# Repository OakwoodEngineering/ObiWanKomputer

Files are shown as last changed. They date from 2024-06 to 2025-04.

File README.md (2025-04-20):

# Obi Wan Komputer and Combined Payload Board
## Oakwood Engineering, NyanSat Project

Welcome to the public git repository for NyanSat's OBC and payload board.  We hope that this project will be generally useful for the CubeSat community.  NyanSat is a 2U CubeSat selected by NASA's CubeSat Launch Initiative and made by high school students at [Oakwood School](https://oakwoodway.org).

[NyanSat Obi Wan Komputer and Combined Payload Board](https://github.com/OakwoodEngineering/ObiWanKomputer) by [Oakwood Engineering](https://nyansat.org) is licensed under [Creative Commons Attribution-ShareAlike 4.0 International](https://creativecommons.org/licenses/by-sa/4.0/?ref=chooser-v1)    

It is based on the [PyCubed](https://pycubed.org) flight computer by Max Holliday.

The design was made with [Kicad EDA](https://www.kicad.org/) version 8 and is in the hardware directory.  More details to come.

For now, an overview of the design is in the following poster presented at Cal Poly's [CubeSat Developer Workshop](https://www.cubesatdw.org/) 2025 (click for PDF):

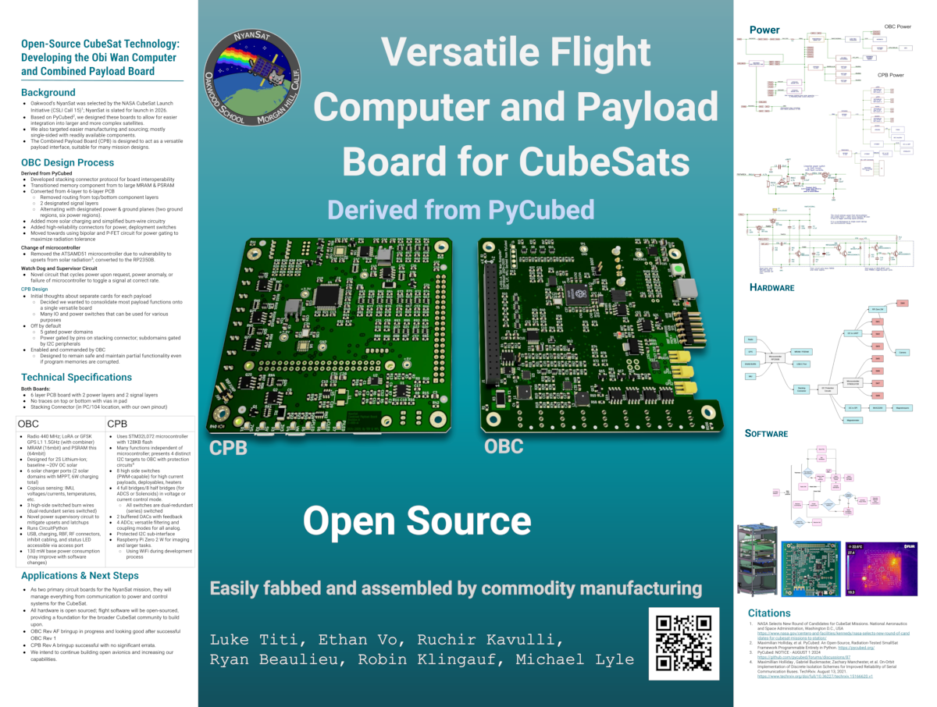
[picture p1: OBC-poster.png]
OBC Poster


You can also visit our website at [nyansat.org](https://nyansat.org).

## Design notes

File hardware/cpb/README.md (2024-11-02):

# NyanSat
## Combined Payload Board

The Combined Payload Board (CPB) is a component of the NyanSat project, designed to interface with a variety of payloads, including imaging, material science experiments, the Attitude Determination and Control Subsystem (ADACS), and the acoustic spacecraft mapping subsystem.

### Internal Interfaces
* Mechanical: PC/104 form factor for holes and board outline.
    * SMT components all on bottom side of board; top side for connectors and stacking Raspberry Pi Zero 2W.
* 40 pin spacecraft electrical bus
	* Battery voltage (post-inhibit switches, current sensing, current limiting on OBC).
	* One GPIO: Gating of battery voltage to board except bridge driver
    * One GPIO: Gating of battery voltage to bridge driver
	* I2C
		* I2C-UART Address: `0x90 = 1001 0000`
            * Raspberry Pi: controlled by serial from I2C-UART.
            * Pi power controlled by I2C-UART GPIO
            * 3 external power switches controlled by I2C-UART GPIOs.
        * I2C-SPI converter for driver bridges `0x50 = 0101 000X`
            * MAX22200 bridge chip select, command select, and enable controlled by I2C-SPI converter.
		* Microcontroller Address: TBD
	* Ground/return path for power and all signals
* Mounting holes
	* 0603 pads from holes to board ground exist; can populate with capacitor (AC-couple to stack), resistor, short, or leave open.

### External Interfaces
* 4 versatile analog inputs. provided by microcontroller ADC, 0-3.3V 12 bit 1.1MSPS.  Pads on board allow selections of various modes:
	* Divided voltage or pulled towards chosen voltage
	* Resistive termination or known impedance
	* AC coupling
    * Pin alternate functions allow use for digital inputs or timer outputs
* 2 DC (0-5V) or AC-coupled waveform generation channels produced from microcontroller DAC with ~40mA drive capability
	* Controlled by microcontroller; feedback to ADC allows precise control of voltages.
	* Low pass filter: 2nd order with -3dB bandwidth of 100KHz.
* 8 high-side switches of battery voltage for payloads and magnetorquers
	* 3 controlled by GPIO from I2C-UART peripheral
	* 1 controlled by onboard Raspberry Pi computer
	* 4 controlled by onboard Cortex-M0+ microcontroller
* 8 half-bridges with programmable current limits
* 5 pin connection for external I2C peripheral (e.g. magnetometer)
* On Pi: CSI interface for Raspberry Pi camera

### Anticipated Use
* Attitude Determination and Control Subsystem (ADACS):
	* Switches: 3 magnetorquers, bipolar (6 half-bridges)
* Acoustic Spacecraft Sounding:
	* Switch: Solenoid, driven by pair of half-bridges
	* Possible switch: MEMS microphone power
	* ADC: 2 channels of MEMS microphone.
* Material science / semiconductor characterization experiment  
	* Waveform generation: 2 channels of drive voltages.
	* ADC: 2 channels of measurement.
* Camera
	* Pi/CSI to camera.
	* Possible high powered LED via high side driver.
* Deployables
	* Option open to use high-side switches channels from here for deployment.
	* Consider using this board to energize second deployable resistor for redundancy.

### Stored-Program Computing Components
* Microcontroller; used mostly as a smart ADC/DAC.
	* STM32L072RBT6; 32MHz Cortex-M0+ with single-cycle multiplier, 128k flash, 6k data EEPROM, 20k RAM.
* Raspberry Pi Zero 2W; used mostly as interface for camera.
	* Quad-core Cortex A53 64-bit processor, 512MB SDRAM.
	* Wireless capabilities (disabled in flight) can be used for ground troubleshooting.
	* Use SLC microSD card, e.g. SFSD2048N1BN1WI-E-QF-111-STD from SwissBit.

### Design Philosophy
* Board's power is gated and will be completely de-powered if a pin on spacecraft electrical bus is not driven high.
* Seperate power gate for magnetorquer full-bridge.
* No high-level sequencing of experiments performed by this board; enabled and commanded from main On-Board Computer (OBC).
* I2C is isolated from spacecraft bus if de-powered or peripheral locks up.
* Large portions of functionality work even if non-volatile memory on a device is corrupted.
	* I2C-UART/GPIO chip does not have nonvolatile memory, and directly controls 4 output switches.
    * I2C-SPI and MAX22200 do not have nonvolatile state.
	* Microcontroller starts up held in reset until explicitly enabled by I2C-UART.
	* If microcontroller is corrupted, Raspberry Pi is capable of reprogramming via on-chip debug features.
    * Pi's power supply is separately enabled by I2C-UART.
	* If Pi filesystem is corrupted, small chance of recovery through failsafe pin (indicates to boot from different part of SD card).

### Known Weaknesses & Shortcomings
* No provision to measure power used by this board.
* No real current limiting beyond master current limiting from ADM1176 PMIC on OBC.
	* But: If entire satellite resets due to overcurrent, this board will revert to default state (turned off).
    * 200 mohm resistors and FET Rds do provide a little bit of mitigation of catastrophes.
* Raspberry Pi must be turned on to generate waveforms / run matsci experiment due to board architecture (needs 5V rail).
* Only having 4 ADC is a little limiting.

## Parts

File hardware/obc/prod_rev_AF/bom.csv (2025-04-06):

Designator | Footprint | Quantity | Value | LCSC Part #
C1, C12 | 0603 | 2 | 3.3nF | C1613
C10, C2, C28, C46, C49, C50, C6, C61, C65 | 0603 | 9 | 4.7uF | C19666
C11, C17, C21, C29, C31, C33, C36, C37, C38, C39, C40, C41, C42, C43, C44, C45, C47, C48, C52, C54, C59, C60, C9 | 0603 | 23 | 0.1uF | C1591
C13, C22, C3, C30 | 0603 | 4 | 10nF | C1589
C14, C16, C34, C51, C55, C62, C7 | 0603 | 7 | 1uF | C59782
C15, C23 | 0603 | 2 | 10uF35V | C194427
C18, C19, C35, C4, C56, C67, C68 | 0603 | 7 | 22uF | C2762594
C20, C24, C25 | 0603 | 3 | 15pF | C107037
C26, C8 | 0603 | 2 | 2.2uF | C23630
C27, C5 | 0603 | 2 | 22nF | C21122
C32 | 0805 | 1 | 47uF | C124129
C53, C57, C58, C64, C66 | 0603 | 5 | 10uF | C344022
C63 | 0603 | 1 | 47nF | C1622
D1 | D_SOD-323 | 1 | BAT20JFILM | C155590
D2 | 0805 | 1 | RED | C84256
D3 | LED_WS2812B_PLCC4_5.0x5.0mm_P3.2mm | 1 | WS2812B-B/W | C2874885
D4 | 0805 | 1 | GREEN | C2297
H1, H2, H3, H4 | MountingHole_3.2mm_M3_DIN965_Pad | 4 | MountingHole_Pad
J1 | PinHeader_2x20_P2.54mm_Vertical | 1 | Conn_02x20_Odd_Even
J2 | PinHeader_1x02_P2.00mm_Vertical | 1 | Conn_01x02
J3 | PinHeader_1x05_P2.54mm_Vertical | 1 | Conn_01x05
J301 | MMCX-6_UMPT-06-01-L-RA-WT-TR_P2.0mm | 1 | Inhibit Switches
J302 | Harwin_G125-FV104F3-02AB000P_P1.25mm_Vertical | 1 | Battery Pack
J4 | PinHeader_1x02_P2.00mm_Vertical | 1 | Conn_01x02
J5 | SAMTEC_MMCXV-J-P-HF-ST-EM1 | 1 | GPS2
J6 | SAMTEC_MMCXV-J-P-HF-ST-EM1 | 1 | GPS1
J7 | SAMTEC_MMCXV-J-P-HF-ST-EM1 | 1 | RADIO
J8 | PinHeader_1x06_P2.54mm_Horizontal | 1 | Conn_01x06
J9 | USB_C_Receptacle_G-Switch_GT-USB-7010ASV | 1 | USB_C_Receptacle_USB2.0 | C2988369
JP300 | CONN_22-11-2032_MOL | 1 | VBURN1
JP301 | CONN_22-11-2032_MOL | 1 | VBURN2
JP302 | CONN_22-11-2032_MOL | 1 | VBURN3
JP303, JP304, JP305 | CONN_22-11-2032_MOL | 3 | VS
JP306, JP307, JP308 | CONN_22-11-2032_MOL | 3 | VS2
L1, L3 | TDK VLCF5020T-330MR62-1 | 2 | 33uH | C2043695
L2, L5 | L_TDK_1008_2.5x2.0mm | 2 | 3.3uH | C404805
L4 | L_pol_2016 | 1 | 3.3uH | C42411119
Q1 | SOIC-8_3.9x4.9mm_P1.27mm | 1 | IRF7306 | C537809
Q10, Q2, Q4, Q6 | SOT-363_SC-70-6 | 4 | BSS138PS,115 | C193381
Q11, Q3, Q5, Q7, Q8, Q9 | SOT-363_SC-70-6 | 6 | MBT2222ADW1T1 | C157366
Q12, Q13, Q21 | SOT-23 | 3 | PMBT2222A | C23869
Q14, Q16, Q19, Q20, Q22 | SOIC-8_3.9x4.9mm_P1.27mm | 5 | IRF9393 | C520642
Q15, Q17, Q18 | SOT-23 | 3 | IRLML2803 | C2590
R1, R106, R107, R2 | 0603 | 4 | DNI
R10, R33, R53, R7 | 0603 | 4 | 680 | C112310
R100, R105, R11, R13, R14, R16, R25, R26, R27, R35, R42, R46, R52, R64, R66, R67, R72, R78, R8, R82, R84, R91, R92, R93 | 0603 | 24 | 10k | C191124
R101, R104 | 0603 | 2 | 5.1k | C105580
R102, R103, R54, R65, R74 | 0603 | 5 | 27 | C137753
R12, R31 | 0603 | 2 | 47 | C114623
R15, R22, R23, R47, R50, R6, R75, R80, R81, R88, R9 | 0603 | 11 | 100K | C5369222
R17, R18 | 0603 | 2 | 34.8k
R19, R43 | 0603 | 2 | 121K | C861095
R20, R60 | 0603 | 2 | 2.1M | C2085910
R21, R51 | 0603 | 2 | 47k | C105579
R24, R32, R41, R59 | 0603 | 4 | 200K | C118142
R28, R34 | 0603 | 2 | 787K | C246008
R29, R36 | 0603 | 2 | 845K | C416579
R3 | 2512 | 1 | 0.1 | C165698
R30, R37, R4 | 0603 | 3 | 220k | C123420
R38, R44, R45, R5, R55, R56, R83, R98 | 0603 | 8 | 1k | C844746
R39 | 0603 | 1 | 73.2K | C843966
R40 | 0603 | 1 | 22.1K | C137768
R48 | 0603 | 1 | 110K | C137807
R49, R57, R58, R63, R68, R69, R71, R73, R77, R87, R89, R90, R96 | 0603 | 13 | 4.7k | C840629
R61 | 0603 | 1 | 316K | C25814
R62, R70 | 0603 | 2 | 3.83k | C482840
R76 | 0603 | 1 | 470 | C114669
R79 | 0603 | 1 | 33 | C108661
R85 | 0603 | 1 | 0 | C100044
R86 | 0603 | 1 | 150 | C336847
R94 | 0603 | 1 | 3.3K | C108078
R95 | 0603 | 1 | 5.23K | C227977
R97 | 0603 | 1 | 1.5k | C193392
R99 | 0603 | 1 | 30.1K | C137745
TP1 | TestPoint_Keystone_5010-5014_Multipurpose | 1 | GND
TP2 | TestPoint_Keystone_5010-5014_Multipurpose | 1 | PACKNEG
U1 | MSOP-10_3x3mm_P0.5mm | 1 | ADM1176-1ARMZ-R7 | C657860
U10 | DQ1225-12-1EP_3.0x3.0mm_P0.51mm | 1 | GP2S1+ | C879828
U11 | QFN50P400X400X100-25N-D | 1 | BQ25886RGER | C2765094
U2 | HTSSOP-14-1EP_4.4x5mm_P0.65mm_EP3.4x5mm_Mask3x3.1mm | 1 | TPS54226PWPRPWP14_2P31X2P46-L | C72066
U3, U5 | QFN-16-1EP_3x3mm_P0.5mm_EP1.9x1.9mm_ThermalVias | 2 | LTC4121 | C687336
U301 | RFM95PW | 1 | RFM98PW
U302 | S1216_24PIN_PACKAGE | 1 | S1216V8
U4 | LGA-16_4.5x3.0mm_P0.5mm | 1 | BMI088 | C194919
U6 | RP2350-QFN-80-1EP_10x10_P0.4mm_EP3.4x3.4mm_ThermalVias | 1 | RP2350_80QFN | C9900138392
U7 | SOIC-8_3.9x4.9mm_P1.27mm | 1 | VTI7064MSME | C139966
U8 | WSON-8-1EP_6x5mm_P1.27mm_EP3.4x4mm | 1 | W25Q128JVPIQ | C190862
U9 | SOT-223-6 | 1 | TPS7A4501DCQT | C2869558
Y1 | Crystal_SMD_3225-4Pin_3.2x2.5mm | 1 | Crystal_GND24_Small | C20625731

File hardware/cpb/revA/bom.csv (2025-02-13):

Designator | Footprint | Quantity | Value | LCSC Part #
C1, C13, C14, C15, C16, C19, C2, C20, C21, C22, C23, C24, C25, C26, C27, C29, C30, C4, C40, C41, C42, C43, C45, C46, C47, C49, C59, C9 | 0603 | 28 | 100nF | C77055
C10, C32, C33, C37, C39, C44, C5 | 0603 | 7 | 2.2uF | C77047
C11, C12 | 0603 | 2 | 68pF | C513699
C17, C18 | 0603 | 2 | 10uF | C85713
C28, C3, C31, C36, C38, C8 | 0805 | 6 | 22uF | C2178186
C34 | 0603 | 1 | 22pF | C326840
C35 | 0603 | 1 | 15pF | C1644
C48 | 0603 | 1 | 1.0uF | C29936
C50 | 0603 | 1 | 22nF | C21122
C51, C52, C53, C54, C55, C56, C57, C58 | 0603 | 8 | 10nF | C100042
C6, C7 | 0603 | 2 | 680pF | C30816
D1 | 0805 | 1 | 7V5 | C84256
D10, D11, D8, D9 | SOT-23 | 4 | MMBZ15VALT1G | C604793
D2 | 0805 | 1 | 5V | C84256
D3 | 0805 | 1 | 3V3 | C84256
D4 | 0805 | 1 | VM | C84256
D5 | 0805 | 1 | GPLED | C2296
D6 | 0805 | 1 | μCLED | C2296
D7 | 0805 | 1 | PILED | C2296
FB1 | 0805 | 1 | BLM21BD272SN1L | C85839
J1 | PinHeader_2x20_P2.54mm_Vertical | 1 | Spacecraft Bus Stacking Connector
J10 | JST_PH_B2B-PH-K_1x02_P2.00mm_Vertical | 1 | SW1
J11 | JST_PH_B2B-PH-K_1x02_P2.00mm_Vertical | 1 | SW2
J12 | JST_PH_B2B-PH-K_1x02_P2.00mm_Vertical | 1 | SW3
J13 | JST_PH_B2B-PH-K_1x02_P2.00mm_Vertical | 1 | PISW1
J14 | JST_PH_B2B-PH-K_1x02_P2.00mm_Vertical | 1 | μSW1
J15 | JST_PH_B2B-PH-K_1x02_P2.00mm_Vertical | 1 | μSW2
J16 | JST_PH_B2B-PH-K_1x02_P2.00mm_Vertical | 1 | μSW3
J17 | JST_PH_B2B-PH-K_1x02_P2.00mm_Vertical | 1 | μSW4
J2 | JST_PH_B5B-PH-K_1x05_P2.00mm_Vertical | 1 | I2CExt
J3 | JST_PH_B3B-PH-K_1x03_P2.00mm_Vertical | 1 | DAC1BUF
J4 | JST_PH_B3B-PH-K_1x03_P2.00mm_Vertical | 1 | DAC2BUF
J6 | RPI02W | 1 | Raspberry Pi Zero 2W
J7 | JST_PH_B5B-PH-K_1x05_P2.00mm_Vertical | 1 | ADC6/7
J8 | JST_PH_B5B-PH-K_1x05_P2.00mm_Vertical | 1 | ADC2/3
J9 | JST_PHD_B8B-PHDSS_2x04_P2.00mm_Vertical | 1 | 4FBRG
J99 | PinHeader_1x02_P2.00mm_Horizontal | 1 | RBFJUMP
L1 | L_Vishay_IHLP-2020 | 1 | 4.7uH | C844991
Q1, Q5, Q7 | SOT-23 | 3 | PMBT2222A | C23869
Q10, Q11, Q14, Q15, Q18, Q19, Q22, Q23 | SOT-363_SC-70-6 | 8 | BSS138PS,115 | C193381
Q12, Q13, Q16, Q17, Q20, Q21, Q24, Q26, Q28, Q30, Q8, Q9 | SOT-363_SC-70-6 | 12 | MBT2222ADW1T1 | C157366
Q2, Q6 | SOIC-8_3.9x4.9mm_P1.27mm | 2 | IRF9393 | C520642
Q25, Q27, Q29, Q31 | SOIC-8_3.9x4.9mm_P1.27mm | 4 | DMP3098LSD | C531177
R1, R47 | 2010 | 2 | 200m 1W | C2073579
R10, R13, R22, R4, R45, R50, R6 | 0603 | 7 | 5.6k | C416722
R100, R101, R102, R103, R96, R97, R98, R99 | 0603 | 8 | 3.3k | C108078
R11, R15, R16, R8 | 0603 | 4 | 0 | C122704
R12, R2, R23, R3, R9 | 0603 | 5 | 3.3k | C844928
R14, R28 | 0603 | 2 | 1.5k | C844921
R17, R54 | 0603 | 2 | 15k | C844742
R18, R29, R30, R37, R38 | 0603 | 5 | 33 | C844553
R19, R31, R32, R48, R49, R51, R58, R59, R68, R69, R78, R79, R88, R89 | 0603 | 14 | 10k | C844918
R20, R21 | 0603 | 2 | 4.7k | C844931
R24, R25, R26, R27, R33, R34, R35, R36, R40, R41, R42, R43 | 0603 | 12 | DNP
R44 | 0603 | 1 | 30k | C844774
R5, R7 | 0603 | 2 | 9.1k | C491147
R56, R57, R66, R67, R76, R77, R86, R87 | 0603 | 8 | 680 | C23228
R60, R61, R70, R71, R80, R81, R90, R91 | 0603 | 8 | 100k | C189597
R62, R63, R72, R73, R82, R83, R92, R93 | 0603 | 8 | 200k | C118142
R64, R65, R74, R75, R84, R85, R94, R95 | 0603 | 8 | 6.8k | C844805
RN1, RN4, RN5, RN6, RN7, RN8, RN9 | R_Array_Convex_4x0603 | 7 | 4.7k | C327044
RN2 | R_Array_Convex_4x0603 | 1 | 1k | C22548
TP1 | TestPoint_Keystone_5010-5014_Multipurpose | 1 | GND
TP2 | TestPoint_Keystone_5010-5014_Multipurpose | 1 | +3.3V
TP3 | TestPoint_Keystone_5010-5014_Multipurpose | 1 | +5V
TP4 | TestPoint_Keystone_5010-5014_Multipurpose | 1 | +7.5V
TP6 | TestPoint_Keystone_5010-5014_Multipurpose | 1 | VM
U1 | SOIC-8_3.9x4.9mm_P1.27mm | 1 | TS912 | C73655
U2 | MSOP-8_3x3mm_P0.65mm | 1 | ADR420ARMZ | C208143
U3, U8 | TO-252-2 | 2 | KF33BDT | C283274
U4 | LQFP-64_10x10mm_P0.5mm | 1 | STM32L072R_B-Z_Tx | C915968
U5 | TSOT-23-6 | 1 | AP62301WU | C3194340
U6 | HVQFN-24-1EP_4x4mm_P0.5mm_EP2.5x2.5mm | 1 | SC16IS750xBS | C2651891
U7 | TSSOP-16_4.4x5mm_P0.65mm | 1 | SC18IS606 | C5190384
U9 | QFN-32-1EP_5x5mm_P0.5mm_EP3.1x3.1mm_ThermalVias | 1 | MAX22200 | C2845158
Y1 | Crystal_SMD_3225-4Pin_3.2x2.5mm | 1 | 14.7456MHz | C2450973

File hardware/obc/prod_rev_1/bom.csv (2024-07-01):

Designator | Footprint | Quantity | Value | LCSC Part #
C101, C102 | 0603 | 2 | 8pF | C1882476
C103, C104, C106, C107, C113, C114, C118, C119, C120, C301, C304, C407 | 0603 | 12 | 0.1uF | C1591
C105, C108, C109, C111, C115, C116, C412, C415 | 0603 | 8 | 1uF | C59782
C110, C112, C117, C404, C405, C413, C417, C421, C601 | 0603 | 9 | 10uF | C85713
C201, C202, C203, C204 | 0603 | 4 | 10nF | C1589
C302 | 0603 | 1 | 150pF | C107038
C303, C416 | 0603 | 2 | 4.7uF | C1705
C305, C401, C402, C411, C419, C420 | 0603 | 6 | 22uF | C84419
C403, C406 | 1210 | 2 | 100uF | C90143
C408 | 0603 | 1 | 2.2uF | C23630
C409 | 0603 | 1 | 22nF | C21122
C410, C414 | 0603 | 2 | 3.3nF | C1613
C418 | 0603 | 1 | 47nF | C1622
D101 | LED_WS2812B_PLCC4_5.0x5.0mm_P3.2mm | 1 | WS2812B-B/W | C114586
D102 | 0805 | 1 | RED | C142306
D402 | 0805 | 1 | GREEN | C2297
D501 | D_SOD-123 | 1 | DFLS130L-7 | C110493
H101, H102, H103, H104 | MountingHole_3.2mm_M3_DIN965_Pad | 4 | MountingHole_Pad
J101 | PinHeader_2x20_P2.54mm_Vertical | 1 | Conn_02x20_Odd_Even
J301 | USB_C_Receptacle_G-Switch_GT-USB-7010ASV | 1 | USB_C_Receptacle_USB2.0 | C2988369
J302 | Harwin_G125-FV104F3-02AB000P_P1.25mm_Vertical | 1 | Conn_High-Rel_4S2P_Vertical
J303 | PinHeader_1x06_P2.54mm_Horizontal | 1 | Conn_01x06
J304 | MMCX-6_UMPT-06-01-L-RA-WT-TR_P2.0mm | 1 | Conn_High-Rel_6P
J305 | PinHeader_1x05_P2.54mm_Vertical | 1 | Conn_01x05
J602, J603, J604 | SAMTEC_MMCXV-J-P-HF-ST-EM1 | 3 | SMA RA Connector
JP401 | SolderJumper-3_P1.3mm_Bridged12_RoundedPad1.0x1.5mm | 1 | Jumper_3_Bridged12
JP501, JP502, JP503, JP504, JP505, JP506, JP507, JP508, JP509 | CONN_22-11-2032_MOL | 9 | Conn_01x03
L101 | L_Sunlord_2.0x1.6mm | 1 | 10uH | C370419
L401 | L_TDK_1008_2.5x2.0mm | 1 | 3.3uH | C404805
L402 | TDK_1008_4.9x5.5mm | 1 | 33uH | C2046704
L403 | 1008 | 1 | 1uH | C5247968
Q201, Q202, Q205, Q206 | SOT-363_SC-70-6 | 4 | BSS138PS,115 | C193381
Q203, Q204, Q207, Q208, Q401, Q402 | SOT-363_SC-70-6 | 6 | MBT2222ADW1T1 | C157366
Q209 | SOT-363_SC-70-6 | 1 | BC857BS,115 | C8654
Q403, Q502, Q503, Q504 | SOT-23 | 4 | IRLML2803 | C2590
Q404, Q505, Q506, Q507 | SO-8_3.9x4.9mm_P1.27mm | 4 | IRF7406PbF | C169769
Q501 | SOT-23 | 1 | MMBT2222AT | C82460
R101 | 0603 | 1 | 680
R102 | 0603 | 1 | 316K | C25814
R103 | 0603 | 1 | 110K | C137807
R104, R105, R106, R108, R114, R205, R206, R207, R209, R215, R216, R217, R219, R301, R302, R402, R422, R426, R427, R430, R501, R502, R503, R504, R601, R602 | 0603 | 26 | 10k | C169849
R107, R226, R423, R429, R505, R506, R507 | 0603 | 7 | 4.7k | C23162
R109, R308 | 0603 | 2 | 150 | C336847
R110, R111, R112, R113 | 0603 | 4 | DNI
R115, R116, R227, R228, R408 | 0603 | 5 | 1K | C844746
R201, R202, R211, R212, R411, R413, R415, R416, R421, R508, R509, R510 | 0603 | 12 | 100K | C5369222
R203, R204, R213, R214 | 0603 | 4 | 680 | C112310
R208, R210, R218, R220, R418 | 0603 | 5 | 200K | C473261
R225, R305, R404 | 0603 | 3 | 0 | C2654002
R303, R304 | 0603 | 2 | 10 | C138286
R306, R307 | 0603 | 2 | 5.1k | C105580
R401 | 0603 | 1 | 107K
R403, R431 | 0603 | 2 | 3.3K | C108078
R405 | 0603 | 1 | 787K | C246008
R406 | 0603 | 1 | 121K | C861095
R407 | 2512 | 1 | 0.1 | C165698
R409, R410 | 0603 | 2 | 73.2K | C843966
R412 | 0603 | 1 | 22.1K | C137768
R414 | 0603 | 1 | 845K | C246013
R417 | 0603 | 1 | 20K | C105575
R419 | 0603 | 1 | 3.01K | C137732
R420 | 0603 | 1 | 2.1M | C2085910
R424 | 0603 | 1 | 5.23K | C227977
R425 | 0603 | 1 | 30.1K | C137745
R428 | 0603 | 1 | 3.16K | C185333
U101 | SO-8_3.9x4.9mm_P1.27mm | 1 | MAX706RESA | C28380
U102 | TQFP-64_10x10mm_P0.5mm | 1 | ATSAMD51J20A-AU | C619371
U103 | LGA-16_4.5x3.0mm_P0.5mm | 1 | BMI088
U301, U302 | UPDFN-8_8.0x6.0mm_P1.27mm | 2 | Mem_MT29F4G01ABAFDWB | C2909506
U401 | SOT-223-6 | 1 | TPS7A4501DCQT | C2869558
U402 | QFN-16-1EP_3x3mm_P0.5mm_EP1.9x1.9mm_ThermalVias | 1 | LTC4121 | C687336
U403 | HTSSOP-14-1EP_4.4x5mm_P0.65mm_EP3.4x5mm_Mask3x3.1mm | 1 | TPS54226PWPRPWP14_2P31X2P46-L | C72066
U404 | MSOP-10_3x3mm_P0.5mm | 1 | ADM1176-1ARMZ-R7 | C657860
U405 | QFN50P400X400X100-25N-D | 1 | BQ25886RGER | C2765094
U501 | RELAY_PE014006_REV-SSE | 1 | PE014006
U601 | RFM95PW | 1 | RFM98PW
U602 | S1216_24PIN_PACKAGE | 1 | S1216V8
U603 | DQ1225-12-1EP_3.0x3.0mm_P0.51mm | 1 | GP2S1+ | C879828
Y101 | Crystal_SMD_3215-2Pin_3.2x1.5mm | 1 | 32.768kHz | C32346

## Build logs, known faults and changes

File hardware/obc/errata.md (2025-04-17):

- Revision 1
    - From PyCubed, CRITICAL: high energy protons cause single-event latchup.  see: https://github.com/pycubed/forums/discussions/87
       > We have found the ATSAMD51 microcontroller used on PyCubed Mainboards (v00 - v05) exhibiting a surprisingly high sensitivity to 50MeV protons. Our KickSat-2 and VR3X missions had zero issues with the ATSAMD51 and the part does have some radiation literature. But after troubleshooting unexplained reboots on our recent PY4 mission, we decided to test it ourselves.
    - Thermal pad for radio is in incorrect mechanical position (mirror image?)
    - Solar charger seems to hit switch current limit when asked to provide 400mA charge to battery.  Need a better inductor (and/or higher switch frequency), and also should choose a current limit with more margin for ripple-- 300-350mA.
    - Have not been able to make GPS work.  GPS enable circuit and UART work, but no satellite lock was achieved.  It was found that due to incorrect pinning, the splitter was installed at a right angle to correct pinout, shorting the signal to ground.
    - Was not able to plug male connectors into MMCXV high-rel RF connectors.  Possble we did not have the correct mating connector, or possible insertion forces are implausibly high.
    - Connector labeling is insufficient.  Need polarity marking and connector purposes.
    - Board coordinate system is probably not correct wrt: satellite coordinate system.
    - U103 pin marking isn't visible with installed part / is under body
    - Too many components require manual rotation during JLCPCB ordering
    - Routing for CHRG# net is pretty terrible
    - Flash chips are not connected to a valid SPI bus on the microcontroller.
    - Our solar arrays could potentially create more than 400mA charge currents, and hit the current limit of the LTC4121.  Consider adding another '4121.
        - The inductor is also oversized, being rated for 1.2A avg current.
    - From JLCPCB DFM review:
        - L101 doesn't fit; substituting 0806 inductor, DFE201610E-100M=P2
          C426327 for order
        - D501 is a pseudo SOD-123 in a power-optimized package but we have
          ordinary SOD-123 pads; substituting 1N5819HW-7-F p/n C82544 for
          order
    - MAX706RESA watchdog timer producing incorrect/unexpected results: the RESET# pin would produce a reset pulse correctly upon powerup when power was toggled (as datasheet indicated), but would then get stuck in a reset loop (RESET# held low) when WDI was held low after the first cycle.
    - No pin 1 marker for radio module on board
    - USB port needs to be accessible through the access port
- Revision AF
    - 4.7k resistor in BOM was out of stock, built with C491210 instead.
    - 845k resistor in BOM incorrect, built with C51263 instead.
    - Components are to close to stacking connector, works for flight but inconvenient on the ground
    - ENHANCEMENTS:
	- Should use a switching power supply for radio to save power
	- Add space for payload castellated modules like original PyCubed

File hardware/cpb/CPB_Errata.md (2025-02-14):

- Revision 1  
    - RN components need proper fanout, some currently have vias in pads which causes marginal clearance.
    - Power Glitch needs to be fixed  
        - C5(22nF) needs to be moved between the gate and +VBATT rather than the gate and ground. (Electrically, everything should remain the same except
for the specified change above).  
    - Q3 doesn't have a base resistor and otherwise needs correction.  After lifting Q3, it is possible to program the microcontroller.
    - DAC outputs noisy.  Need better bypassing of 5V and possibly AVDD supply; consider layout improvements and guard rings.
    - DACs glitch at power up.  May be possible to address with power-up sequence (getting 3V3 going before 5V).
    - Power switches turn off pretty slow, inhibiting PWM.
        - R96 should be a smaller value-- perhaps 1/3rd the value to not waste too much power.
        - Select smaller output FET with lower gate charge.  DMP3098LSD has the same pinout and less than half the gate charge.
        - Between these two changes, we might "turn off" 7-8x as fast.
    - Need to rethink connector pinning.  Do we want to put a supply on ADC headers?
    - ENHANCEMENT: Consider adding a power LED for VM
    - ENHANCEMENT: GPLEDs (amber) could be brighter
    - Erroneous previous errata: Missing pullup for MAX22200 SDO.  MAX22200 SDO is open-drain and cannot drive pin high, but we have no pullup on pin.  (there was actually a pull-up).
- Revision A
    - Documentation: part number for RN2 was incorrect.  Using C93675 instead of the single 0603 that is in the BOM.
    - Documentation: 33 ohm resistors were ordered as C844927 due to shortfall of C844553.
    - Documentation: Some datasheet URLs in BOM were incorrect.

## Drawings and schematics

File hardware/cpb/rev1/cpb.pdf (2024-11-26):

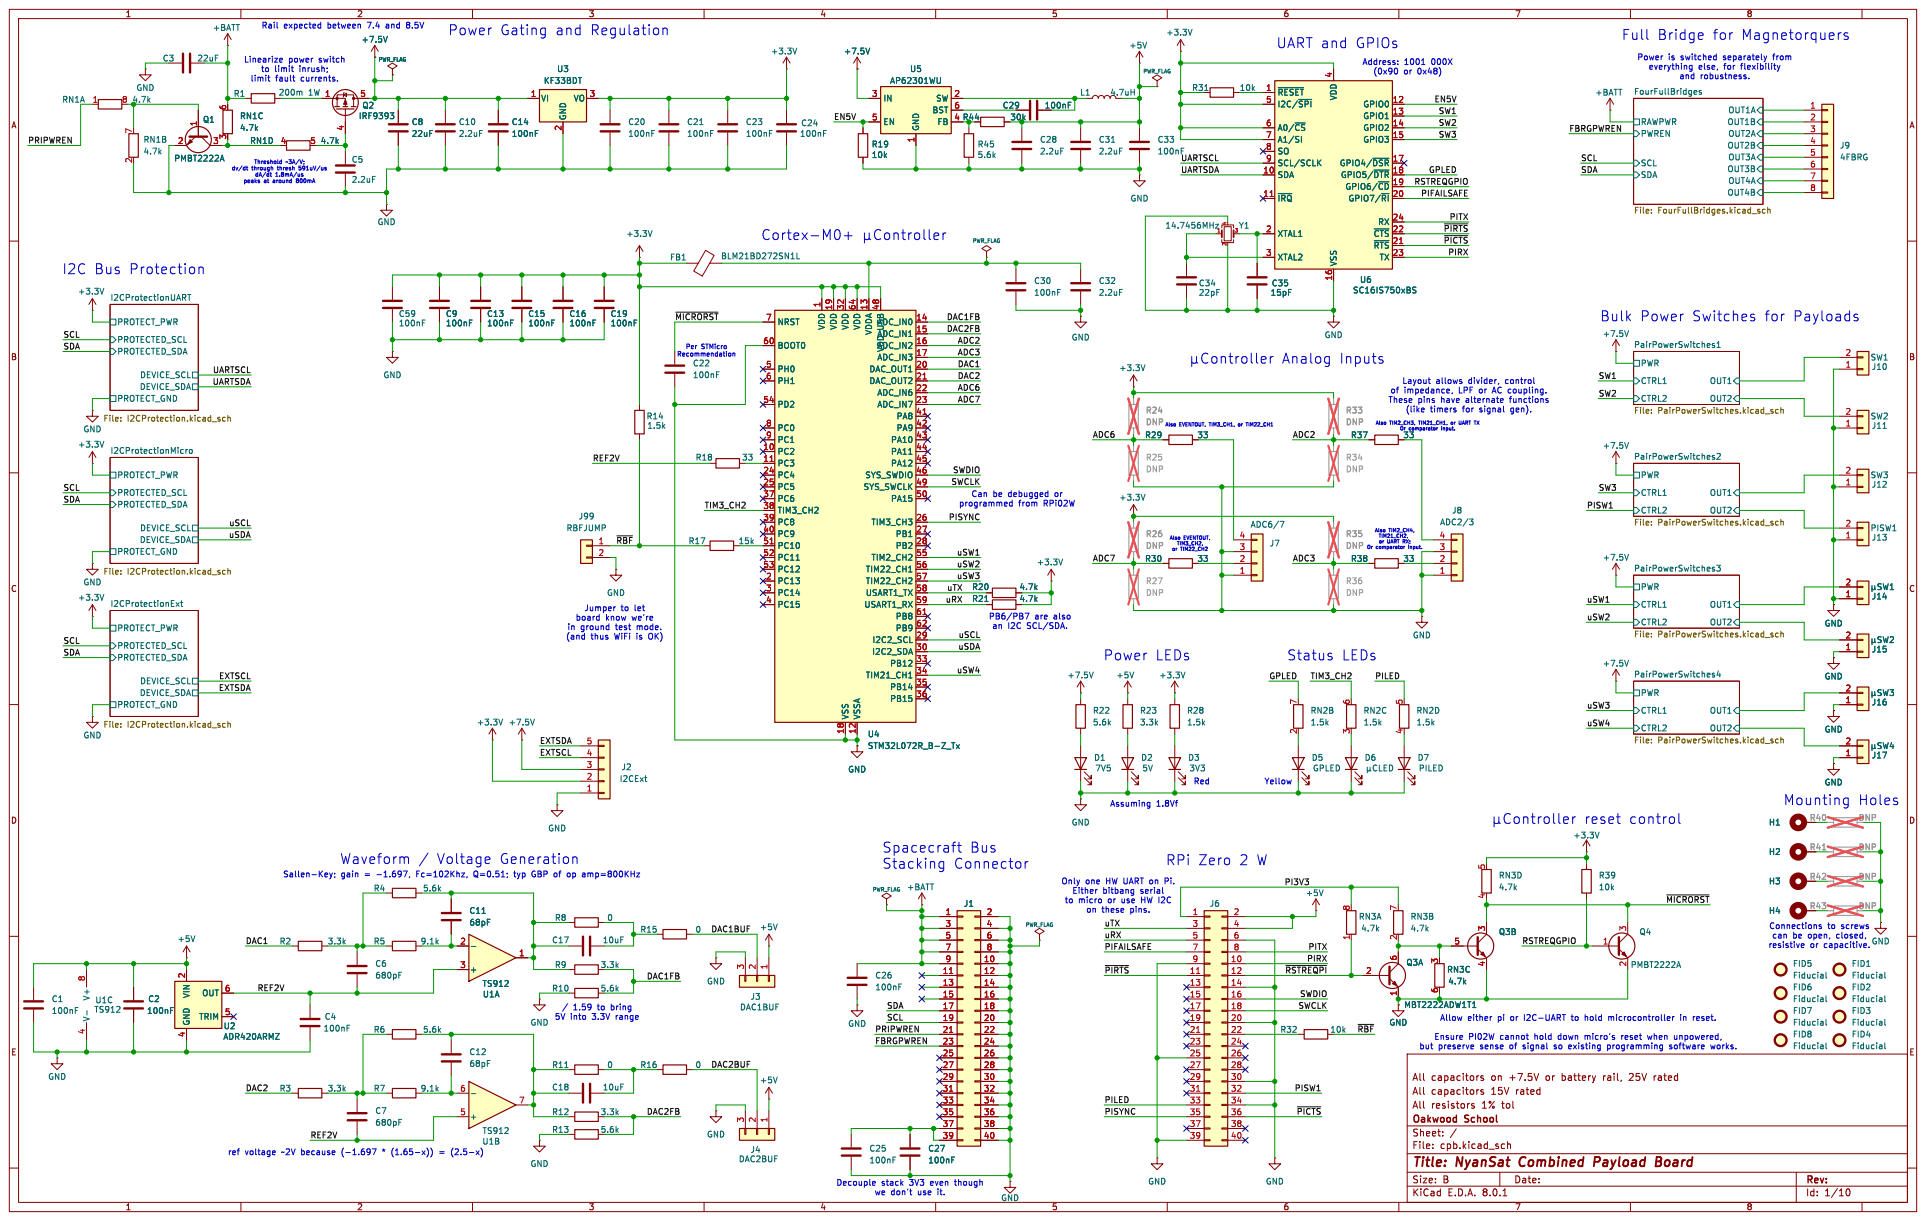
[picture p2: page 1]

limit fault currents. Rail expected between 7.4 and 8.5V

Power Gating and Regulation

Full Bridge for Magnetorquers

1 PC2 10 PC3 11 VSSA 12 VDDA 13 ADC_IN0 14 ADC_IN1 15 ADC_IN2 16 ADC_IN3 17 VSS 18 VDD 19 PC13 2 DAC_OUT1 20 DAC_OUT2 21 ADC_IN6 22 ADC_IN7 23 PC4 24 PC5 25 TIM3_CH3 26 PB1 27 PB2 28

Bulk Power Switches for Payloads

(like timers for signal gen).

Jumper to let board know we're

in ground test mode. (and thus WiFi is OK)

Only one HW UART on Pi. Either bitbang serial to micro or use HW I2C

Id: 1/10 Title: NyanSat Combined Payload Board

Decouple stack 3V3 even though we don't use it.

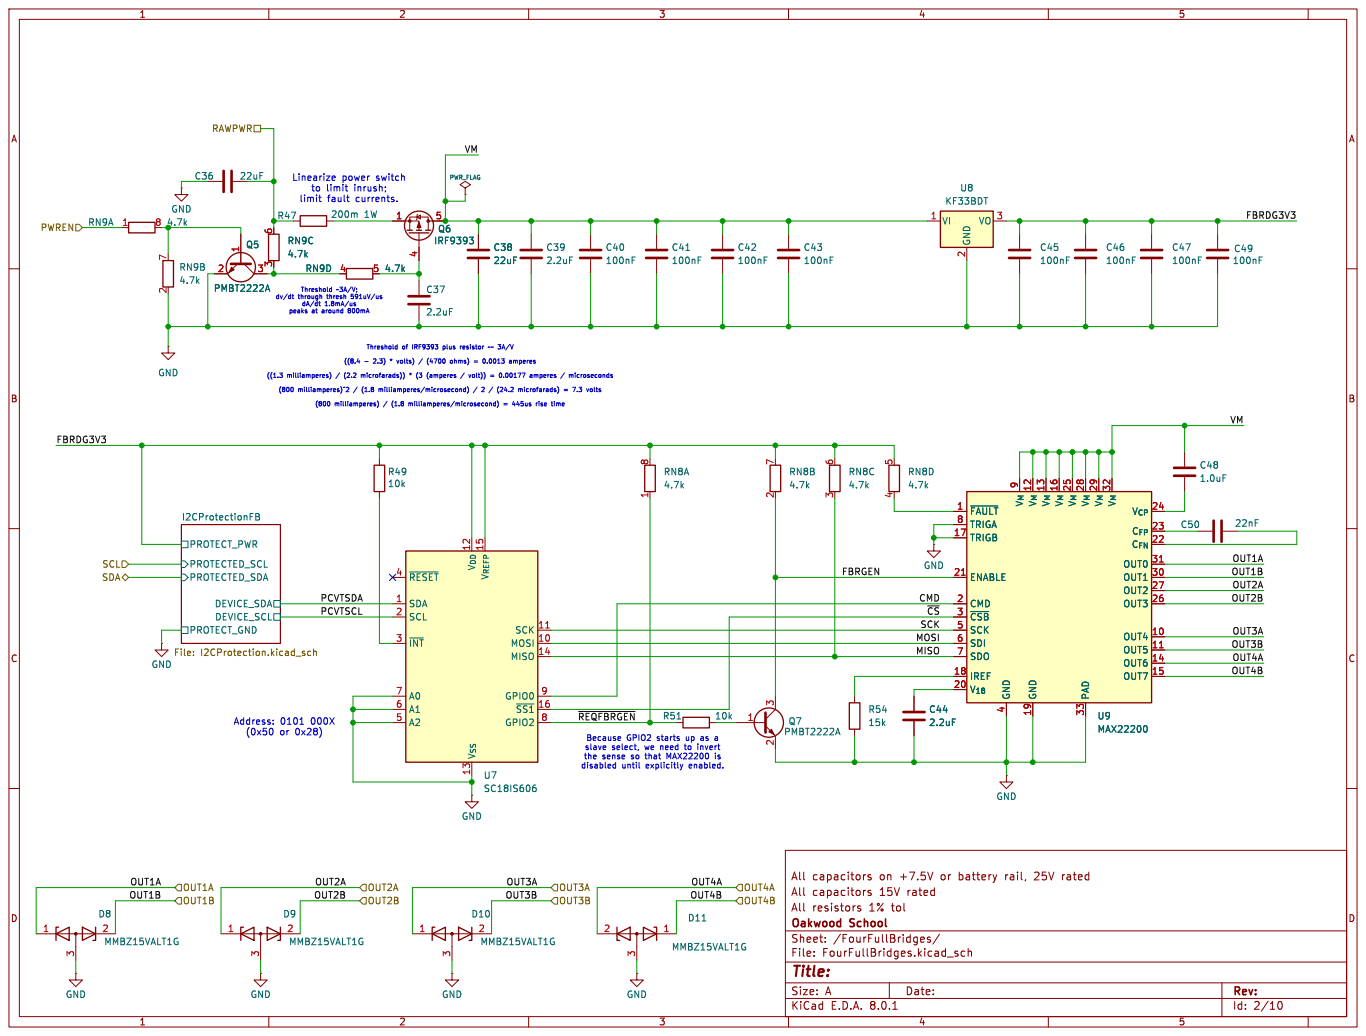
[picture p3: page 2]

4 SCK 5 SDI 6 SDO 7 TRIGA 8 V_{M}9 U9 MAX22200 GNDGND R47 200m 1W

4 SCK 5 SDI 6 SDO 7 TRIGA 8 V_{M}9

slave select, we need to invert

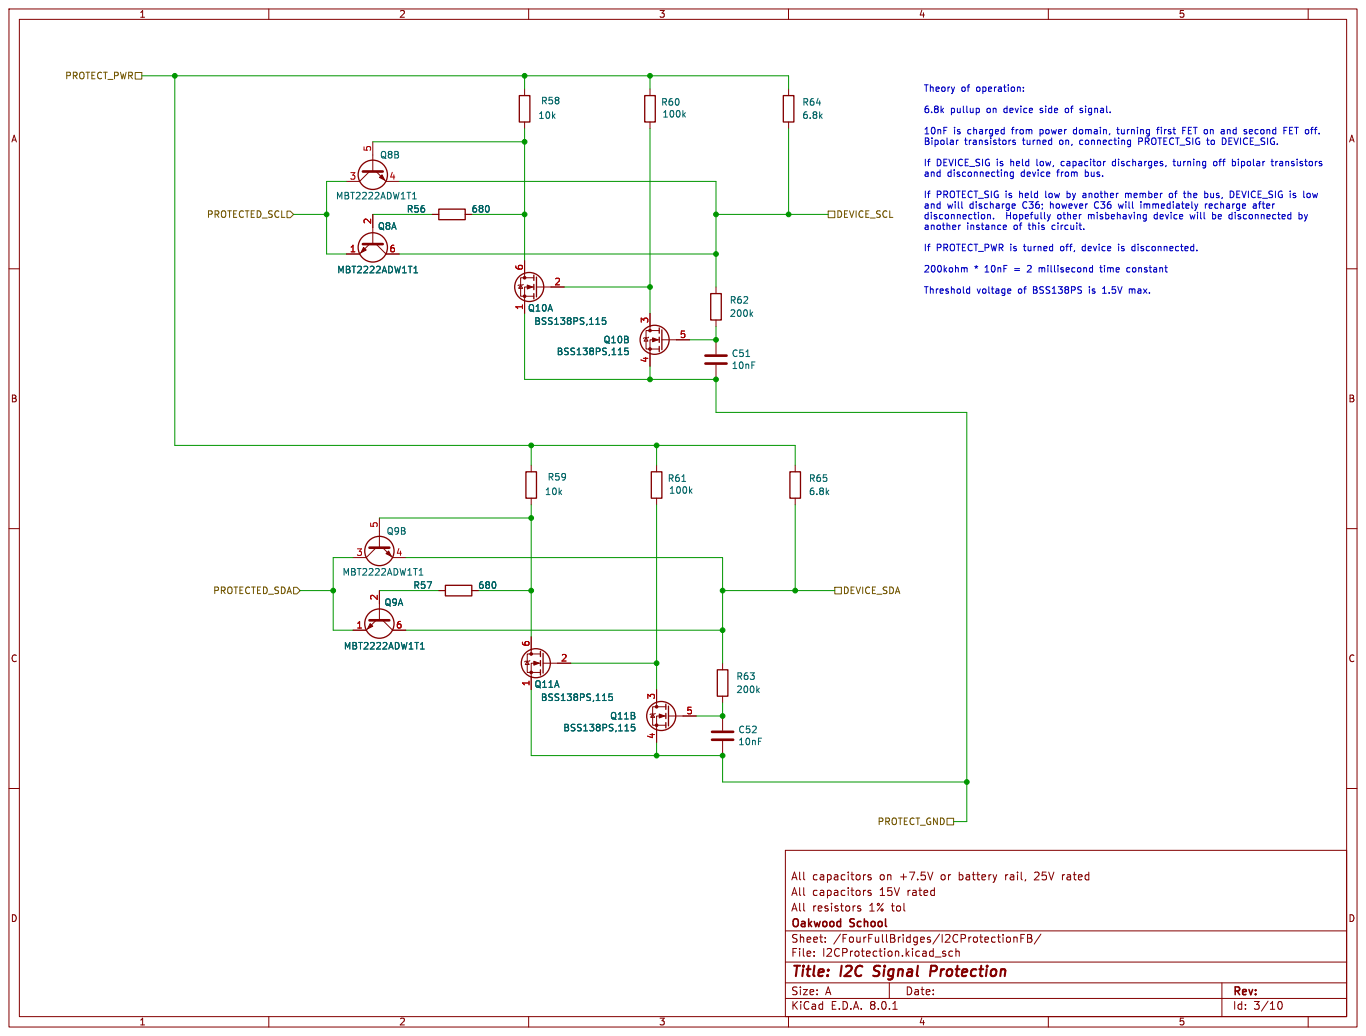
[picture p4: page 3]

If PROTECT_SIG is held low by another member of the bus, DEVICE_SIG is low

Id: 3/10 Title: I2C Signal Protection

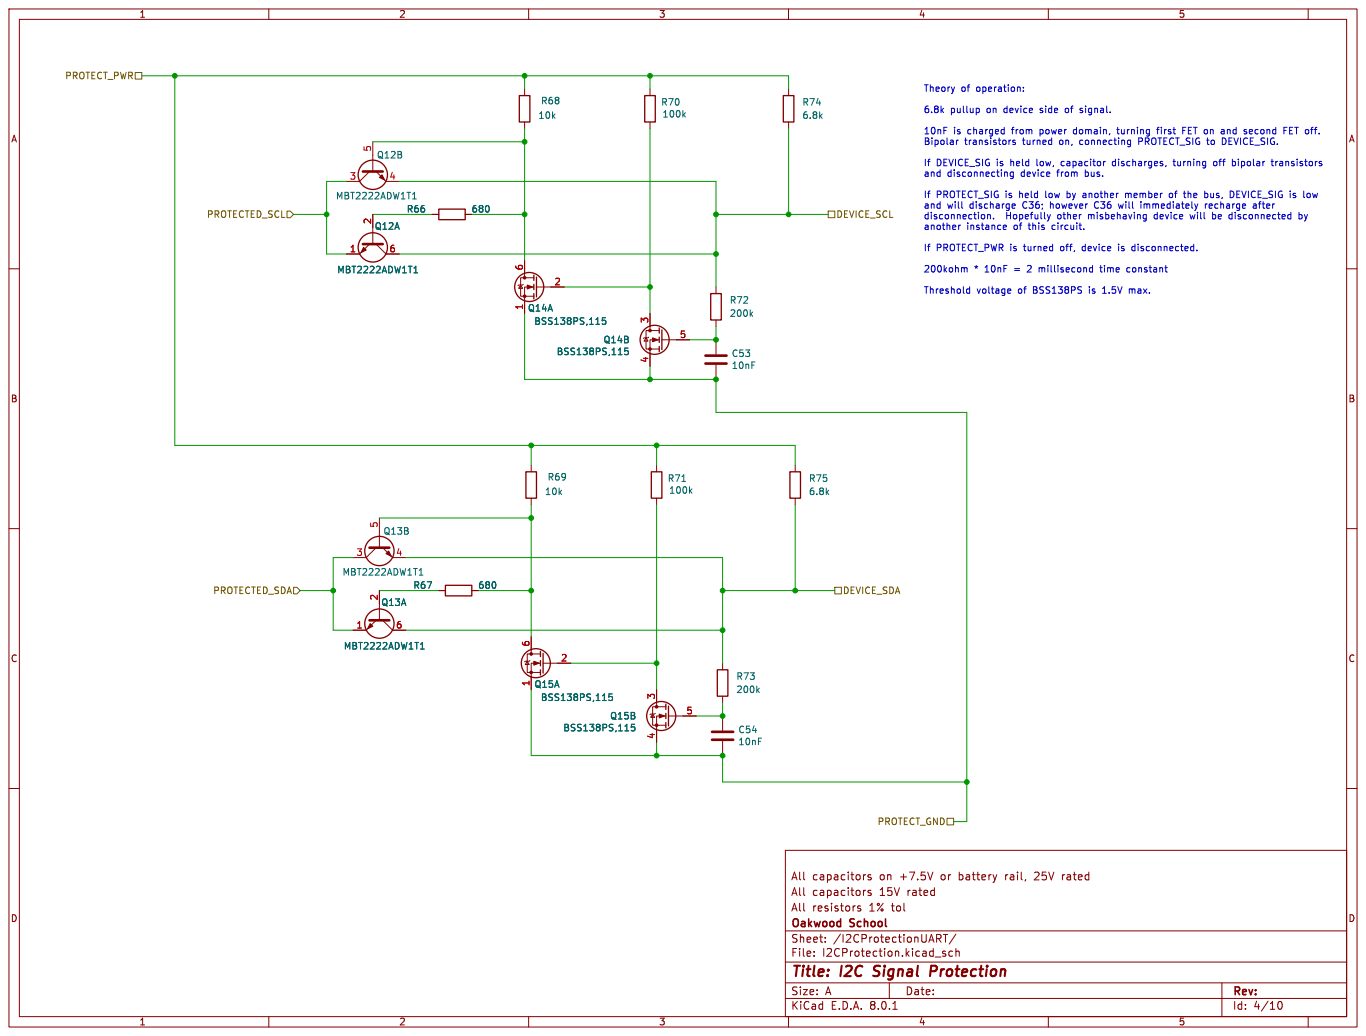
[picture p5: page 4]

If PROTECT_SIG is held low by another member of the bus, DEVICE_SIG is low

Id: 4/10 Title: I2C Signal Protection

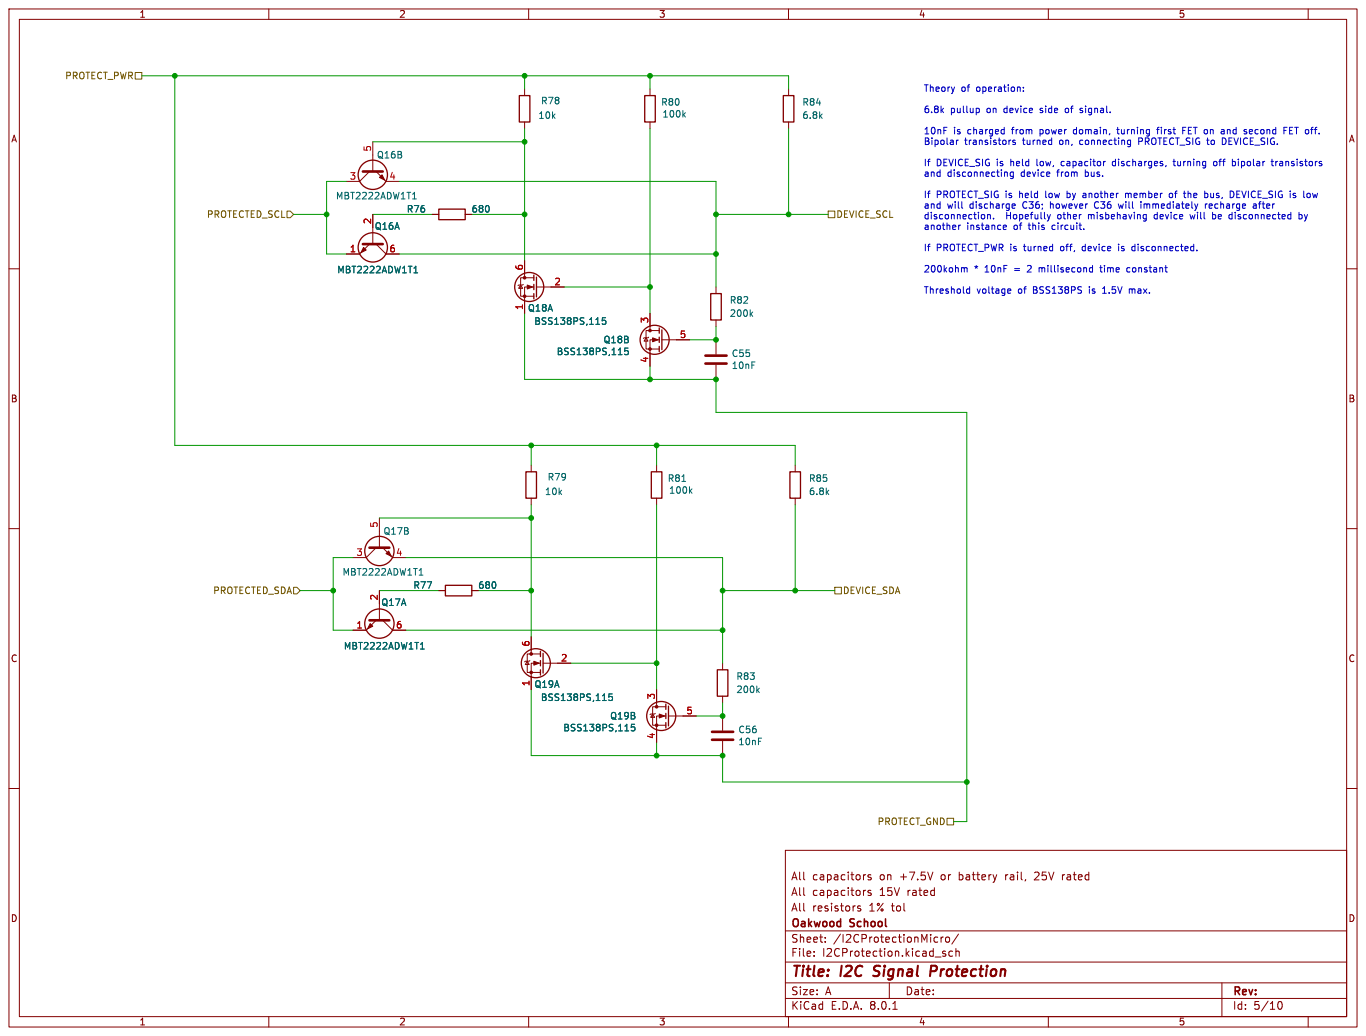
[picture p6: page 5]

If PROTECT_SIG is held low by another member of the bus, DEVICE_SIG is low

Id: 5/10 Title: I2C Signal Protection

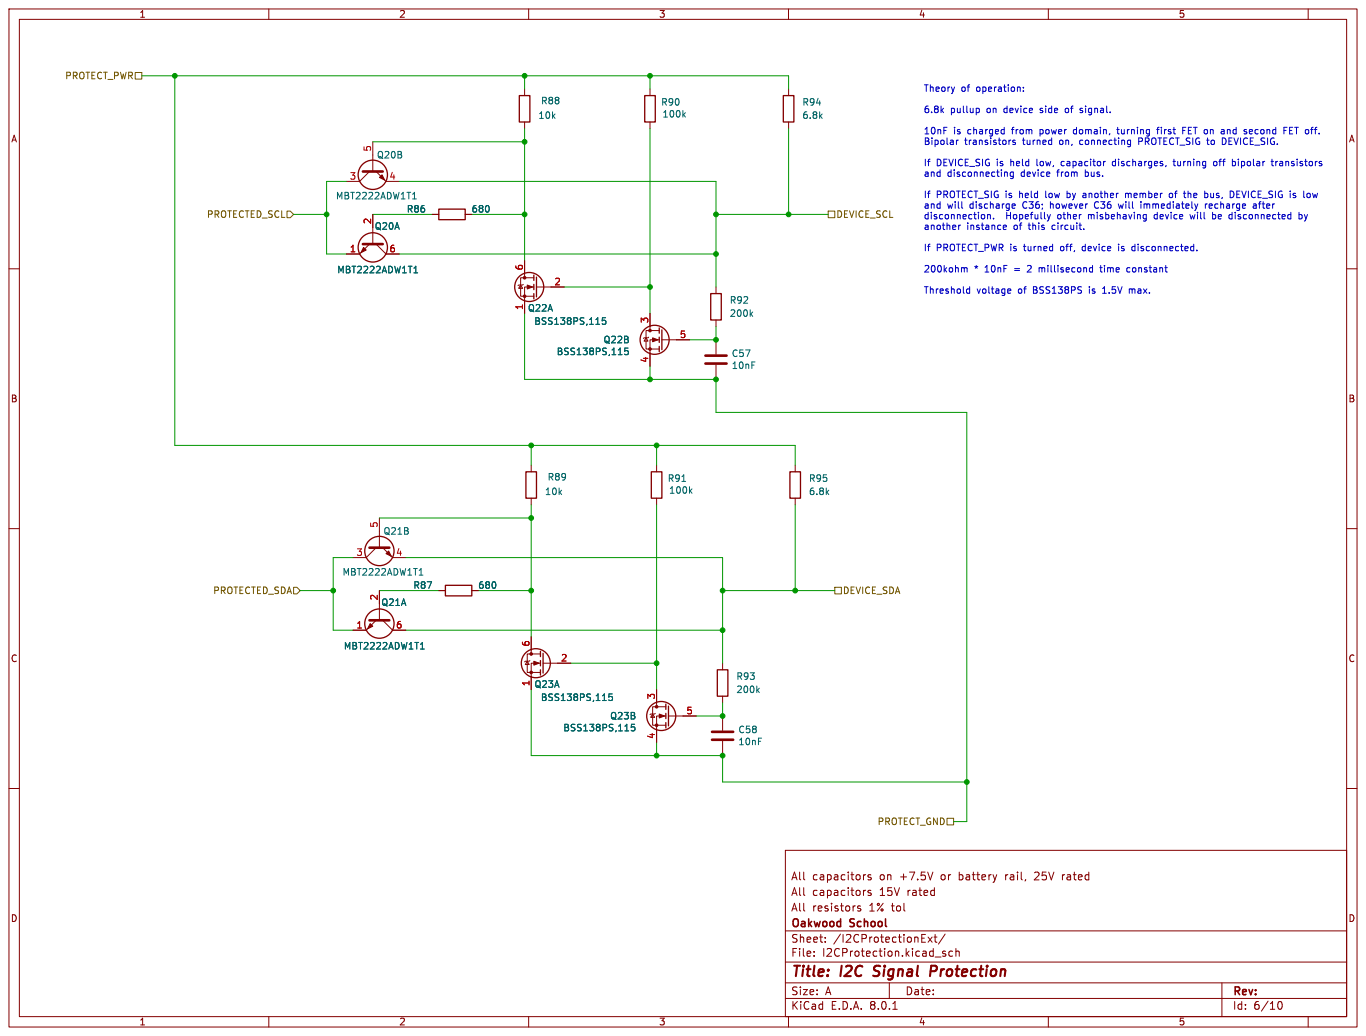
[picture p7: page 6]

If PROTECT_SIG is held low by another member of the bus, DEVICE_SIG is low

Id: 6/10 Title: I2C Signal Protection

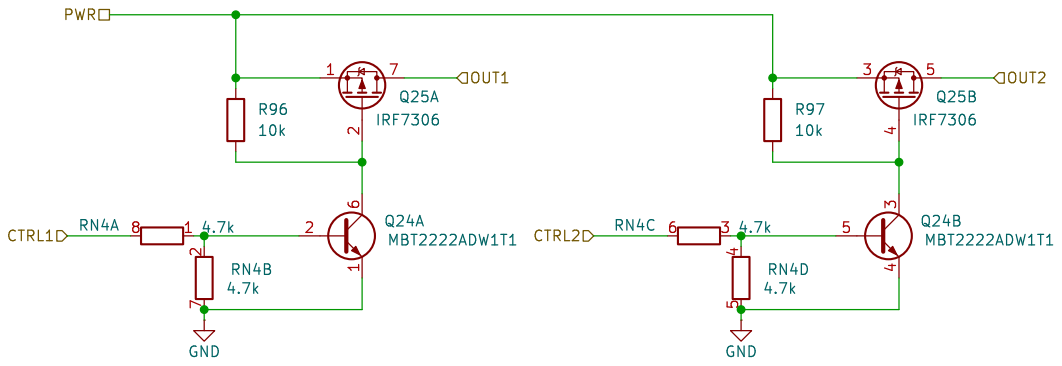
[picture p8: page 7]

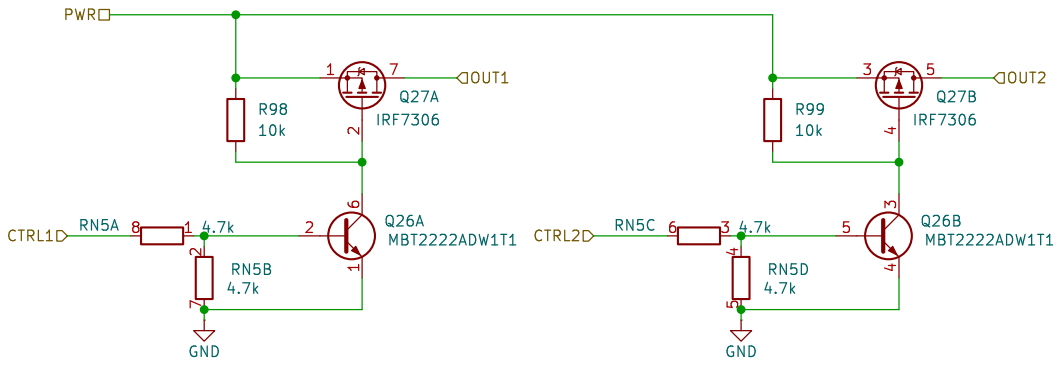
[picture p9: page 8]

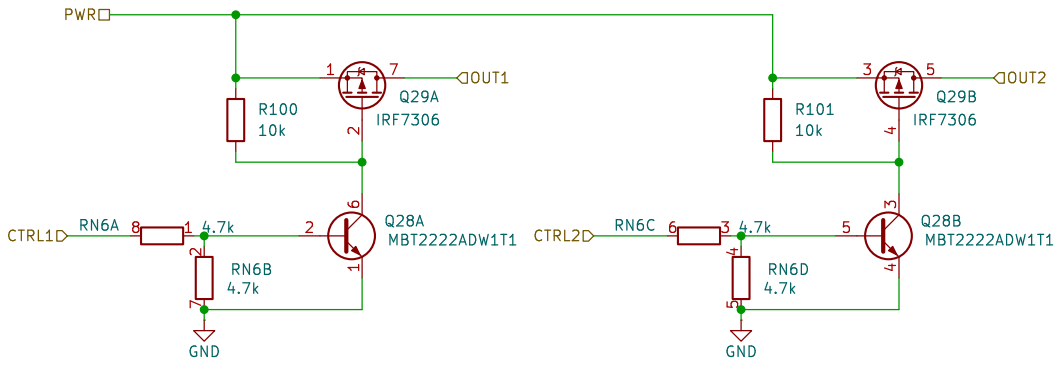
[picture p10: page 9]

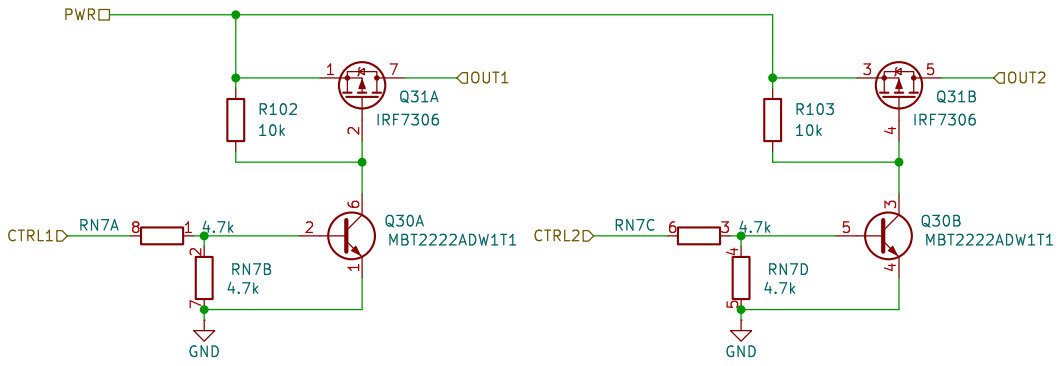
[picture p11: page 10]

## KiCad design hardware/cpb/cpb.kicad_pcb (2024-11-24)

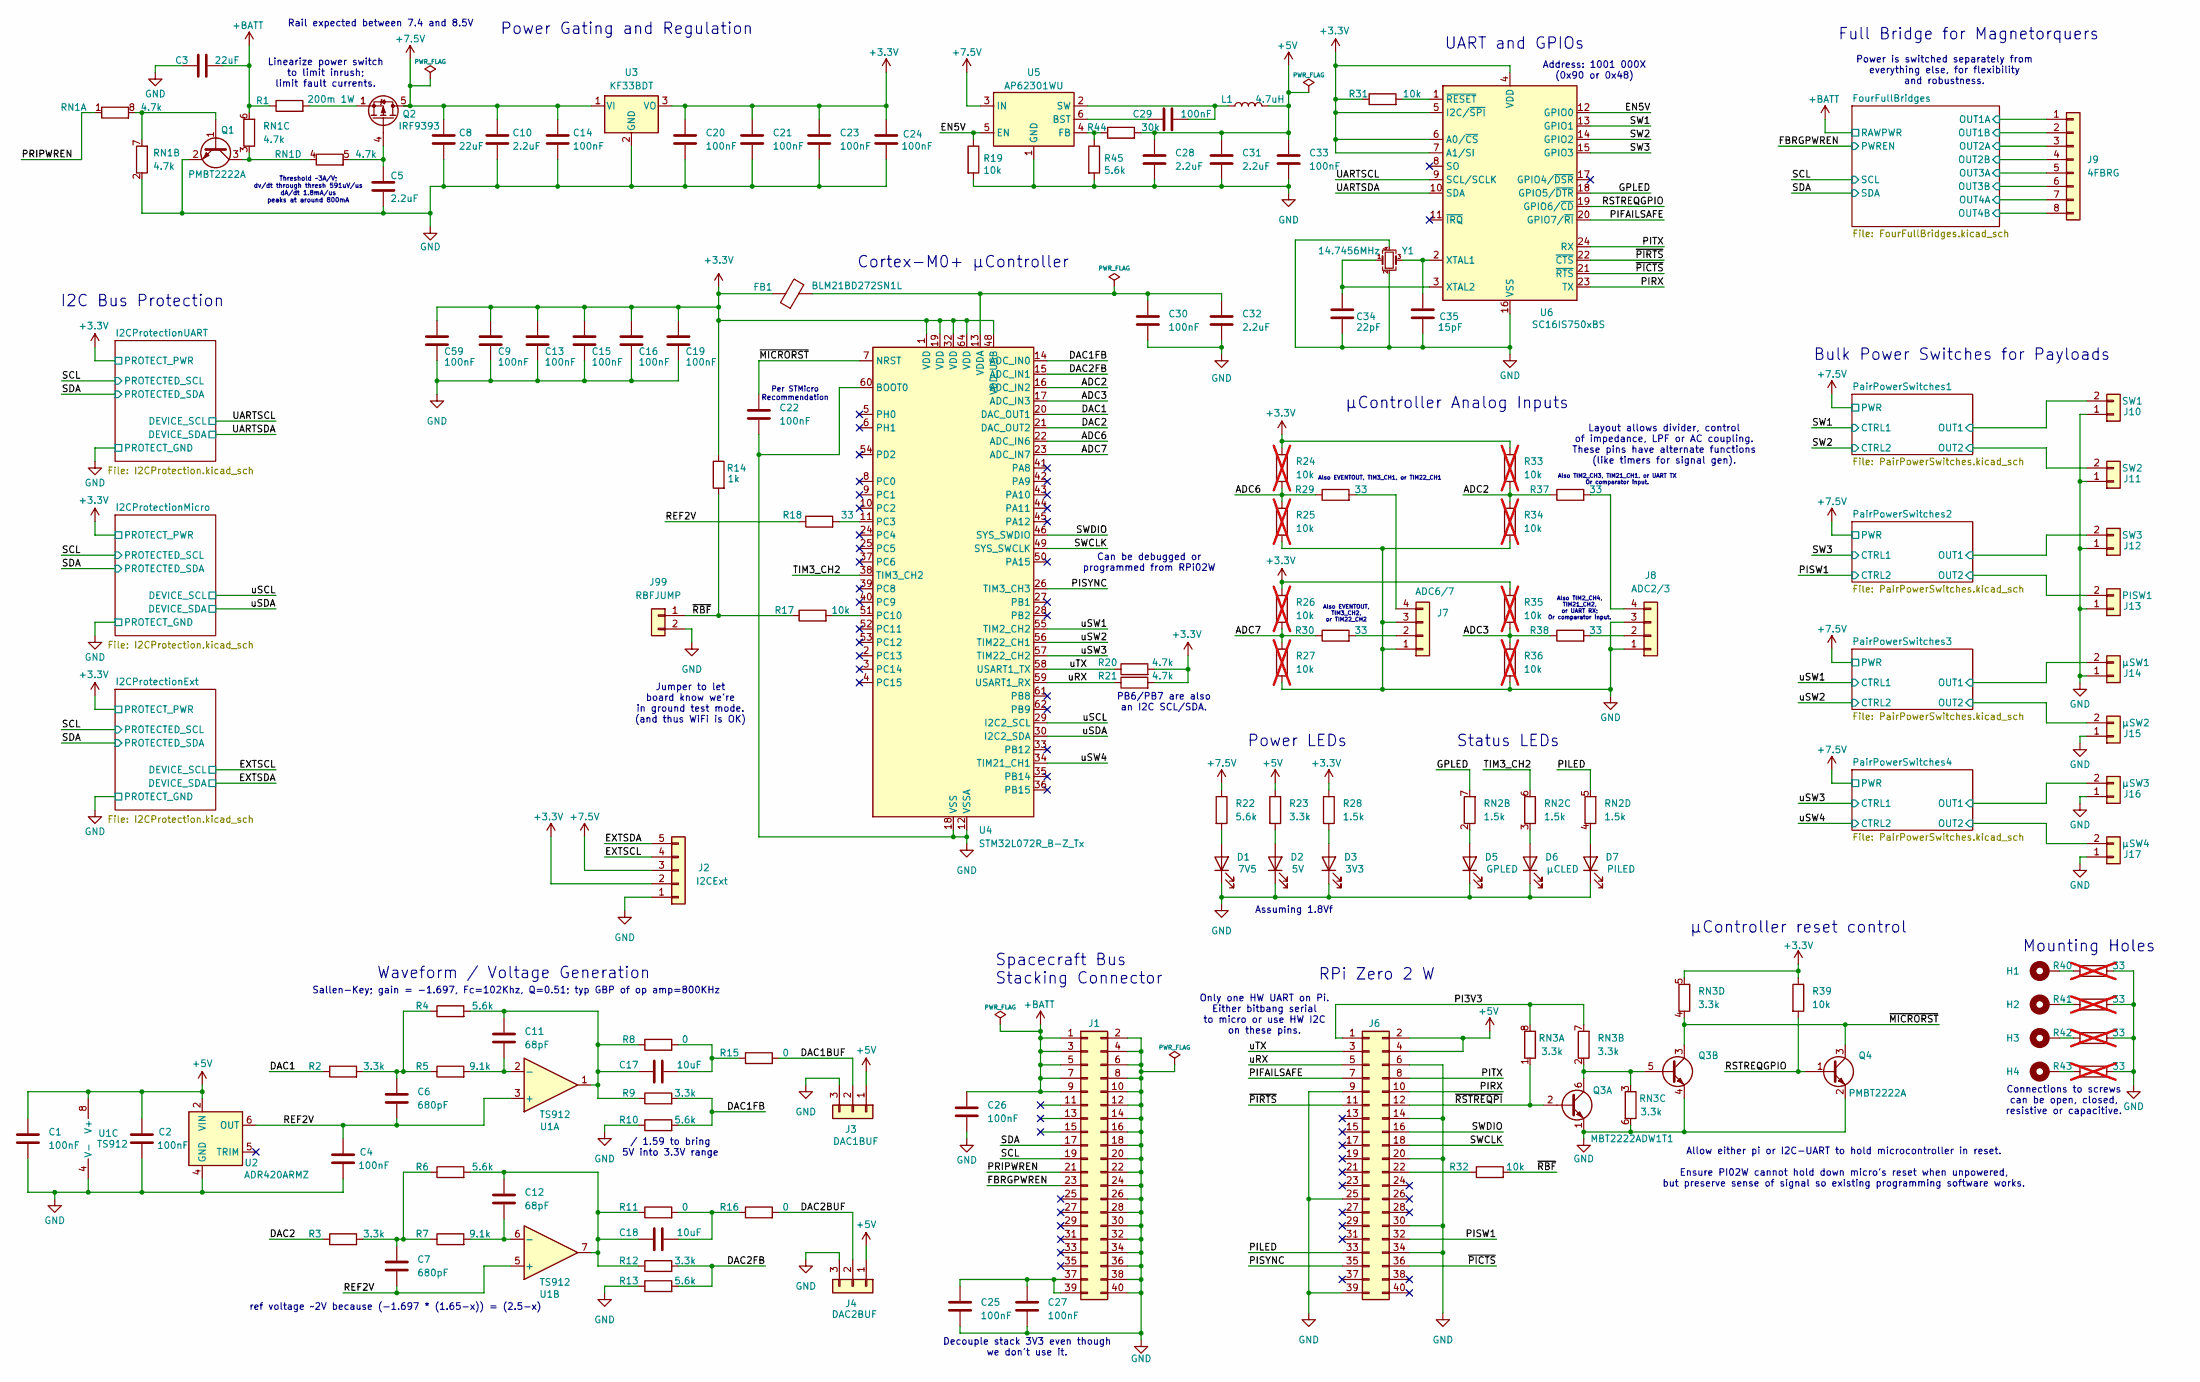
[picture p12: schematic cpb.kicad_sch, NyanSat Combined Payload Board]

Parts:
C1, C2, C4, C9, C13, C14, C15, C16, C19, C20, C21, C22, C23, C24, C25, C26, C27, C29, C30, C33, C59: 100nF; C_0603_1608Metric
C3, C8: 22uF; C_0805_2012Metric
C5, C10, C28, C31, C32: 2.2uF; C_0603_1608Metric
C6, C7: 680pF; C_0603_1608Metric
C11, C12: 68pF; C_0603_1608Metric
C17, C18: 10uF; C_0603_1608Metric
C34: 22pF; C_0603_1608Metric
C35: 15pF; C_0603_1608Metric
D1: 7V5; LED_0805_2012Metric; LCSC C84256
D2: 5V; LED_0805_2012Metric; LCSC C84256
D3: 3V3; LED_0805_2012Metric; LCSC C84256
D5: GPLED; LED_0805_2012Metric; LCSC C84256
D6: μCLED; LED_0805_2012Metric; LCSC C84256
D7: PILED; LED_0805_2012Metric; LCSC C84256
FB1: BLM21BD272SN1L; L_0805_2012Metric; LCSC C85839
H1, H2, H3, H4: MountingHole_Pad; MountingHole_3.2mm_M3_DIN965_Pad
J1: Spacecraft Bus Stacking Connector; PinHeader_2x20_P2.54mm_Vertical
J2: I2CExt; JST_PH_B5B-PH-K_1x05_P2.00mm_Vertical
J3: DAC1BUF; JST_PH_B3B-PH-K_1x03_P2.00mm_Vertical
J4: DAC2BUF; JST_PH_B3B-PH-K_1x03_P2.00mm_Vertical
J6: Raspberry Pi Zero 2W; RPI02W
J7: ADC6/7; JST_PH_B4B-PH-K_1x04_P2.00mm_Vertical
J8: ADC2/3; JST_PH_B4B-PH-K_1x04_P2.00mm_Vertical
J9: 4FBRG; JST_PHD_B8B-PHDSS_2x04_P2.00mm_Vertical
J10: SW1; JST_PH_B2B-PH-K_1x02_P2.00mm_Vertical
J11: SW2; JST_PH_B2B-PH-K_1x02_P2.00mm_Vertical
J12: SW3; JST_PH_B2B-PH-K_1x02_P2.00mm_Vertical
J13: PISW1; JST_PH_B2B-PH-K_1x02_P2.00mm_Vertical
J14: μSW1; JST_PH_B2B-PH-K_1x02_P2.00mm_Vertical
J15: μSW2; JST_PH_B2B-PH-K_1x02_P2.00mm_Vertical
J16: μSW3; JST_PH_B2B-PH-K_1x02_P2.00mm_Vertical
J17: μSW4; JST_PH_B2B-PH-K_1x02_P2.00mm_Vertical
J99: RBFJUMP; SolderJumper-2_P1.3mm_Open_TrianglePad1.0x1.5mm
L1: 4.7uH; L_Vishay_IHLP-2020; LCSC C844991
Q1, Q4: PMBT2222A; SOT-23; LCSC C23869
Q2: IRF9393; SOIC-8_3.9x4.9mm_P1.27mm; LCSC C520642
Q3: MBT2222ADW1T1; SOT-363_SC-70-6; LCSC C157366
R1: 200m 1W; R_1206_3216Metric
R2, R3, R9, R12, R23: 3.3k; R_0603_1608Metric
R4, R6, R10, R13, R22, R45: 5.6k; R_0603_1608Metric
R5, R7: 9.1k; R_0603_1608Metric
R8, R11, R15, R16: 0; R_0603_1608Metric
R14: 1k; R_0603_1608Metric
R17, R19, R31, R32, R39: 10k; R_0603_1608Metric
R18, R29, R30, R37, R38: 33; R_0603_1608Metric
R20, R21: 4.7k; R_0603_1608Metric
R24, R25, R26, R27, R33, R34, R35, R36: 10k; R_0603_1608Metric; not fitted
R28: 1.5k; R_0603_1608Metric
R40, R41, R42, R43: 33; R_0603_1608Metric; not fitted
R44: 30k; R_0603_1608Metric
RN1: 4.7k; R_Array_Convex_4x0603
RN2: 1.5k; R_Array_Convex_4x0603
RN3: 3.3k; R_Array_Convex_4x0603
U1: TS912; SOIC-8_3.9x4.9mm_P1.27mm; LCSC C73655
U2: ADR420ARMZ; MSOP-8_3x3mm_P0.65mm; LCSC C208143
U3: KF33BDT; TO-252-2; LCSC C283274
U4: STM32L072R_B-Z_Tx; LQFP-64_10x10mm_P0.5mm; LCSC C915968
U5: AP62301WU; TSOT-23-6
U6: SC16IS750xBS; HVQFN-24-1EP_4x4mm_P0.5mm_EP2.5x2.5mm; LCSC C2651891
Y1: 14.7456MHz; Crystal_SMD_3225-4Pin_3.2x2.5mm

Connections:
+3.3V: C9.1, C13.1, C15.1, C16.1, C19.1, C20.1, C21.1, C23.1, C24.1, C59.1, FB1.1, J2.2, R14.1, R20.2, R21.2, R24.1, R26.1, R28.1, R31.1, R33.1, R35.1, R39.1, RN3.5 (R4.2), U3.3 (VO), U4.1 (VDD), U4.19 (VDD), U4.32 (VDD), U4.48 (VDD_USB), U4.64 (VDD), U6.4 (VDD), U6.5 (I2C/~SPI), U6.6 (A0/~CS), U6.7 (A1/SI); also elsewhere on the board
+5V: C1.1, C2.1, C28.1, C31.1, C33.1, J3.1, J4.1, J6.2, J6.4, L1.2, R23.1, R44.2, U1.8 (V+), U2.2 (VIN)
+7.5V: C8.1, C10.1, C14.1, J2.3, Q2.5 (D), Q2.6 (D), Q2.7 (D), Q2.8 (D), R22.1, U3.1 (VI), U5.3 (IN); also elsewhere on the board
+BATT: C3.2, C26.1, J1.1, J1.3, J1.5, J1.7, J1.9, R1.1, RN1.6 (R3.2); also elsewhere on the board
/ADC2: R33.2, R34.1, R37.1, U4.16 (ADC_IN2)
/ADC3: R35.2, R36.1, R38.1, U4.17 (ADC_IN3)
/ADC6: R24.2, R25.1, R29.1, U4.22 (ADC_IN6)
/ADC7: R26.2, R27.1, R30.1, U4.23 (ADC_IN7)
/DAC1: R2.1, U4.20 (DAC_OUT1)
/DAC1BUF: J3.2, R15.2
/DAC1FB: R9.2, R10.2, U4.14 (ADC_IN0)
/DAC2: R3.1, U4.21 (DAC_OUT2)
/DAC2BUF: J4.2, R16.2
/DAC2FB: R12.2, R13.2, U4.15 (ADC_IN1)
/EN5V: R19.1, U5.5 (EN), U6.12 (GPIO0)
/EXTSCL: J2.4; also elsewhere on the board
/EXTSDA: J2.5; also elsewhere on the board
/FBRGPWREN: J1.23; also elsewhere on the board
/FourFullBridges/OUT1A: J9.1; also elsewhere on the board
/FourFullBridges/OUT1B: J9.2; also elsewhere on the board
/FourFullBridges/OUT2A: J9.3; also elsewhere on the board
/FourFullBridges/OUT2B: J9.4; also elsewhere on the board
/FourFullBridges/OUT3A: J9.5; also elsewhere on the board
/FourFullBridges/OUT3B: J9.6; also elsewhere on the board
/FourFullBridges/OUT4A: J9.7; also elsewhere on the board
/FourFullBridges/OUT4B: J9.8; also elsewhere on the board
/GPLED: RN2.7 (R2.2), U6.18 (GPIO5/~DTR)
/PI3V3: J6.1, RN3.7 (R2.2), RN3.8 (R1.2)
/PIFAILSAFE: J6.7, U6.20 (GPIO7/~RI)
/PILED: J6.33, RN2.5 (R4.2)
/PIRX: J6.10, U6.23 (TX)
/PISW1: J6.32; also elsewhere on the board
/PISYNC: J6.35, U4.26 (TIM3_CH3)
/PITX: J6.8, U6.24 (RX)
/PRIPWREN: J1.21, RN1.1 (R1.1)
/PairPowerSwitches1/OUT1: J10.2; also elsewhere on the board
/PairPowerSwitches1/OUT2: J11.2; also elsewhere on the board
/PairPowerSwitches2/OUT1: J12.2; also elsewhere on the board
/PairPowerSwitches2/OUT2: J13.2; also elsewhere on the board
/PairPowerSwitches3/OUT1: J14.2; also elsewhere on the board
/PairPowerSwitches3/OUT2: J15.2; also elsewhere on the board
/PairPowerSwitches4/OUT1: J16.2; also elsewhere on the board
/PairPowerSwitches4/OUT2: J17.2; also elsewhere on the board
/REF2V: C4.1, C6.2, C7.2, R18.1, U1.3 (+), U1.5 (+), U2.6 (OUT)
/RSTREQGPIO: Q4.1 (B), R39.2, U6.19 (GPIO6/~CD)
/SCL: J1.19; also elsewhere on the board
/SDA: J1.17; also elsewhere on the board
/SW1: U6.13 (GPIO1); also elsewhere on the board
/SW2: U6.14 (GPIO2); also elsewhere on the board
/SW3: U6.15 (GPIO3); also elsewhere on the board
/SWCLK: J6.18, U4.49 (SYS_SWCLK)
/SWDIO: J6.16, U4.46 (SYS_SWDIO)
/TIM3_CH2: RN2.6 (R3.2), U4.38 (TIM3_CH2)
/UARTSCL: U6.9 (SCL/SCLK); also elsewhere on the board
/UARTSDA: U6.10 (SDA); also elsewhere on the board
/uRX: J6.5, R21.1, U4.59 (USART1_RX)
/uSCL: U4.29 (I2C2_SCL); also elsewhere on the board
/uSDA: U4.30 (I2C2_SDA); also elsewhere on the board
/uSW1: U4.55 (TIM2_CH2); also elsewhere on the board
/uSW2: U4.56 (TIM22_CH1); also elsewhere on the board
/uSW3: U4.57 (TIM22_CH2); also elsewhere on the board
/uSW4: U4.34 (TIM21_CH1); also elsewhere on the board
/uTX: J6.3, R20.1, U4.58 (USART1_TX)
/~MICRORST: C22.1, Q3.3 (C2), Q4.3 (C), RN3.4 (R4.1), U4.7 (NRST)
/~PICTS: J6.36, U6.21 (~RTS)
/~PIRTS: J6.11, U6.22 (~CTS)
/~RBF: J99.1, R14.2, R17.1, R32.2
/~RSTREQPI: J6.12, Q3.2 (B1), RN3.1 (R1.1)
GND: C1.2, C2.2, C3.1, C4.2, C5.2, C8.2, C9.2, C10.2, C13.2, C14.2, C15.2, C16.2, C19.2, C20.2, C21.2, C22.2, C23.2, C24.2, C25.2, C26.2, C27.2, C28.2, C30.2, C31.2, C32.2, C33.2, C34.2, C35.2, C59.2, D1.1 (K), D2.1 (K), D3.1 (K), D5.1 (K), D6.1 (K), D7.1 (K), J1.2, J1.4, J1.6, J1.8, J1.10, J1.12, J1.14, J1.16, J1.18, J1.20, J1.22, J1.24, J1.26, J1.28, J1.30, J1.32, J1.34, J1.36, J1.38, J1.40, J2.1, J3.3, J4.3, J6.6, J6.9, J6.14, J6.20, J6.25, J6.30, J6.34, J6.39, J7.1, J7.3, J8.1, J8.3, J10.1, J11.1, J12.1, J13.1, J14.1, J15.1, J16.1, J17.1, J99.2, Q1.2 (E), Q3.1 (E1), Q3.4 (E2), Q4.2 (E), R10.1, R13.1, R19.2, R25.2, R27.2, R34.2, R36.2, R40.2, R41.2, R42.2, R43.2, R45.2, RN1.2 (R2.1), RN3.6 (R3.2), U1.4 (V-), U2.4 (GND), U3.2 (GND), U4.12 (VSSA), U4.18 (VSS), U4.31 (VSS), U4.47 (VSS), U4.60 (BOOT0), U4.63 (VSS), U5.1 (GND), U6.16 (VSS), U6.25 (VSS), Y1.2, Y1.4; also elsewhere on the board
unnamed: C6.1, R2.2, R4.1, R5.1
unnamed: C7.1, R3.2, R6.1, R7.1
unnamed: C11.1, C17.1, R4.2, R8.1, R9.1, U1.1
unnamed: C12.1, C18.1, R6.2, R11.1, R12.1, U1.7
unnamed: C17.2, R8.2, R15.1
unnamed: C18.2, R11.2, R16.1
unnamed: D1.2 (A), R22.2
unnamed: D2.2 (A), R23.2
unnamed: D3.2 (A), R28.2
unnamed: D5.2 (A), RN2.2 (R2.1)
unnamed: D6.2 (A), RN2.3 (R3.1)
unnamed: D7.2 (A), RN2.4 (R4.1)
unnamed: H1.1, R40.1
unnamed: H2.1, R41.1
unnamed: H3.1, R42.1
unnamed: H4.1, R43.1
unnamed: C25.1, C27.1, J1.37, J1.39
unnamed: J6.22, R32.1
unnamed: J7.2, R30.2
unnamed: J7.4, R29.2
unnamed: J8.2, R38.2
unnamed: J8.4, R37.2
unnamed: Q1.1 (B), RN1.7 (R2.2), RN1.8 (R1.2)
unnamed: Q1.3 (C), RN1.3 (R3.1), RN1.4 (R4.1)
unnamed: C5.1, Q2.4 (G), RN1.5 (R4.2)
unnamed: Q2.1 (S), Q2.2 (S), Q2.3 (S), R1.2
unnamed: Q3.5 (B2), Q3.6 (C1), RN3.2 (R2.1), RN3.3 (R3.1)
unnamed: C11.2, R5.2, U1.2 (-)
unnamed: C12.2, R7.2, U1.6 (-)
unnamed: R18.2, U4.11 (PC3)
unnamed: R17.2, U4.51 (PC10)
unnamed: C30.1, C32.1, FB1.2, U4.13 (VDDA)
unnamed: C29.1, U5.6 (BST)
unnamed: R44.1, R45.1, U5.4 (FB)
unnamed: C29.2, L1.1, U5.2 (SW)
unnamed: C35.1, U6.2 (XTAL1), Y1.3
unnamed: C34.1, U6.3 (XTAL2), Y1.1
unnamed: R31.2, U6.1 (~RESET)

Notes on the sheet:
Also TIM2_CH3, TIM21_CH1, or UART TX Or comparator input.
Bulk Power Switches for Payloads
Connections to screws can be open, closed, resistive or capacitive.
μController Analog Inputs
Power LEDs
Can be debugged or programmed from RPi02W
Allow either pi or I2C-UART to hold microcontroller in reset. Ensure PI02W cannot hold down micro's reset when unpowered, but preserve sense of signal so existing programming software works.
Threshold ~3A/V; dv/dt through thresh 591uV/us dA/dt 1.8mA/us peaks at around 800mA
Only one HW UART on Pi. Either bitbang serial to micro or use HW I2C on these pins.
Decouple stack 3V3 even though we don't use it.
Power Gating and Regulation
ref voltage ~2V because (-1.697 * (1.65-x)) = (2.5-x)
PB6/PB7 are also an I2C SCL/SDA.
Also TIM2_CH4, TIM21_CH2, or UART RX; Or comparator input.
Rail expected between 7.4 and 8.5V
Power is switched separately from everything else, for flexibility and robustness.
Mounting Holes
μController reset control
Sallen-Key; gain = -1.697, Fc=102Khz, Q=0.51; typ GBP of op amp=800KHz
RPi Zero 2 W
Assuming 1.8Vf
Also EVENTOUT, TIM3_CH2, or TIM22_CH2
Layout allows divider, control of impedance, LPF or AC coupling. These pins have alternate functions (like timers for signal gen).
Address: 1001 000X (0x90 or 0x48)
Status LEDs
UART and GPIOs
Linearize power switch to limit inrush; limit fault currents.
Jumper to let board know we're in ground test mode. (and thus WiFi is OK)
Per STMicro Recommendation
/ 1.59 to bring 5V into 3.3V range
Spacecraft Bus Stacking Connector
Also EVENTOUT, TIM3_CH1, or TIM22_CH1
Waveform / Voltage Generation
Cortex-M0+ μController
Full Bridge for Magnetorquers
I2C Bus Protection

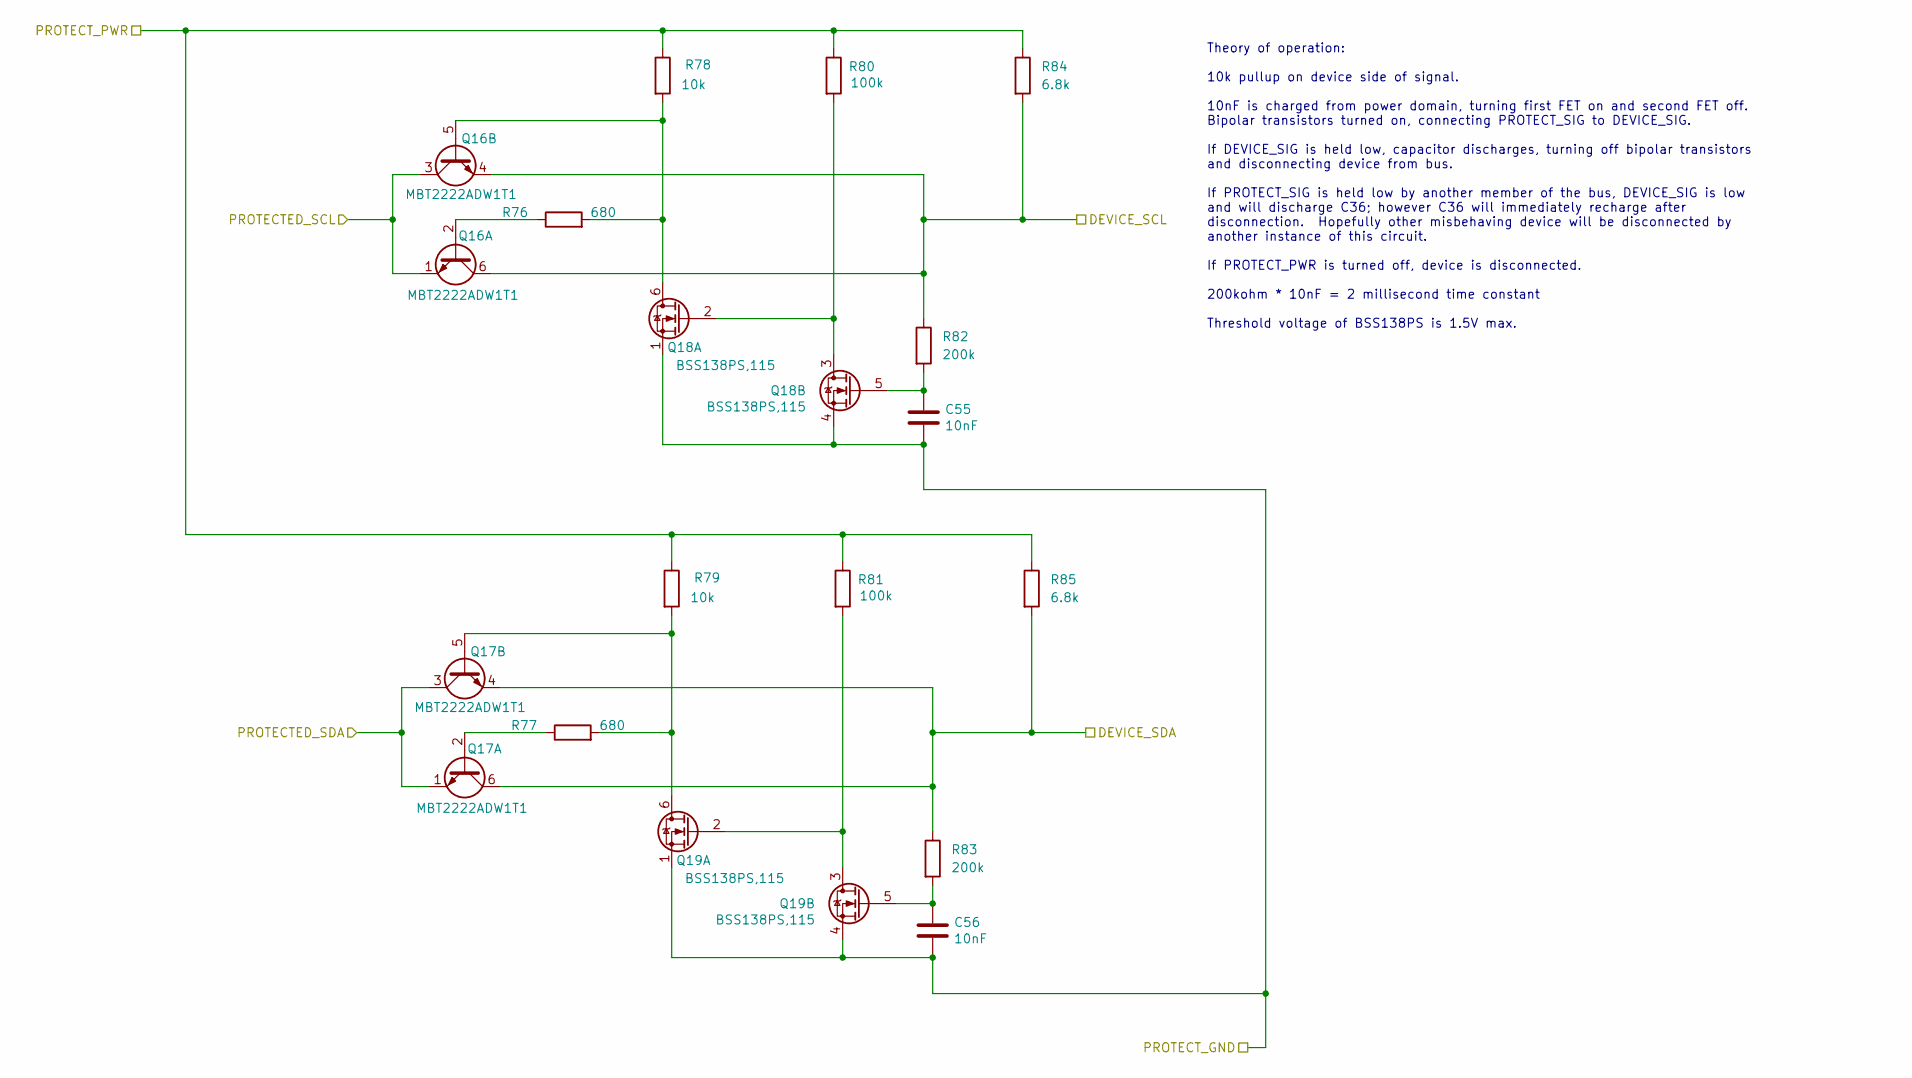
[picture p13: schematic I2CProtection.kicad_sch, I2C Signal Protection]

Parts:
C55, C56: 10nF; C_0603_1608Metric
Q16, Q17: MBT2222ADW1T1; SOT-363_SC-70-6; LCSC C157366
Q18, Q19: BSS138PS,115; SOT-363_SC-70-6; LCSC C193381
R76, R77: 680; R_0603_1608Metric
R78, R79: 10k; R_0603_1608Metric
R80, R81: 100k; R_0603_1608Metric
R82, R83: 200k; R_0603_1608Metric
R84, R85: 6.8k; R_0603_1608Metric

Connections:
+3.3V: R78.1, R79.1, R80.1, R81.1, R84.1, R85.1; also elsewhere on the board
/SCL: Q16.1 (E1), Q16.3 (C2); also elsewhere on the board
/SDA: Q17.1 (E1), Q17.3 (C2); also elsewhere on the board
/uSCL: Q16.4 (E2), Q16.6 (C1), R82.1, R84.2; also elsewhere on the board
/uSDA: Q17.4 (E2), Q17.6 (C1), R83.1, R85.2; also elsewhere on the board
GND: C55.2, C56.2, Q18.1 (S2), Q18.4 (S1), Q19.1 (S2), Q19.4 (S1); also elsewhere on the board
unnamed: Q16.2 (B1), R76.1
unnamed: Q16.5 (B2), Q18.6 (D1), R76.2, R78.2
unnamed: Q17.2 (B1), R77.1
unnamed: Q17.5 (B2), Q19.6 (D1), R77.2, R79.2
unnamed: Q18.2 (G2), Q18.3 (D2), R80.2
unnamed: C55.1, Q18.5 (G1), R82.2
unnamed: Q19.2 (G2), Q19.3 (D2), R81.2
unnamed: C56.1, Q19.5 (G1), R83.2

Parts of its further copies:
C51, C52, C53, C54, C57, C58: 10nF; C_0603_1608Metric
Q8, Q9, Q12, Q13, Q20, Q21: MBT2222ADW1T1; SOT-363_SC-70-6; LCSC C157366
Q10, Q11, Q14, Q15, Q22, Q23: BSS138PS,115; SOT-363_SC-70-6; LCSC C193381
R56, R57, R66, R67, R86, R87: 680; R_0603_1608Metric
R58, R59, R68, R69, R88, R89: 10k; R_0603_1608Metric
R60, R61, R70, R71, R90, R91: 100k; R_0603_1608Metric
R62, R63, R72, R73, R92, R93: 200k; R_0603_1608Metric
R64, R65, R74, R75, R94, R95: 6.8k; R_0603_1608Metric

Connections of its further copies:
+3.3V: R68.1, R69.1, R70.1, R71.1, R74.1, R75.1, R88.1, R89.1, R90.1, R91.1, R94.1, R95.1; also elsewhere on the board
/EXTSCL: Q20.4 (E2), Q20.6 (C1), R92.1, R94.2; also elsewhere on the board
/EXTSDA: Q21.4 (E2), Q21.6 (C1), R93.1, R95.2; also elsewhere on the board
/FourFullBridges/FBRDG3V3: R58.1, R59.1, R60.1, R61.1, R64.1, R65.1; also elsewhere on the board
/FourFullBridges/PCVTSCL: Q8.4 (E2), Q8.6 (C1), R62.1, R64.2; also elsewhere on the board
/FourFullBridges/PCVTSDA: Q9.4 (E2), Q9.6 (C1), R63.1, R65.2; also elsewhere on the board
/SCL: Q8.1 (E1), Q8.3 (C2), Q12.1 (E1), Q12.3 (C2), Q20.1 (E1), Q20.3 (C2); also elsewhere on the board
/SDA: Q9.1 (E1), Q9.3 (C2), Q13.1 (E1), Q13.3 (C2), Q21.1 (E1), Q21.3 (C2); also elsewhere on the board
/UARTSCL: Q12.4 (E2), Q12.6 (C1), R72.1, R74.2; also elsewhere on the board
/UARTSDA: Q13.4 (E2), Q13.6 (C1), R73.1, R75.2; also elsewhere on the board
GND: C51.2, C52.2, C53.2, C54.2, C57.2, C58.2, Q10.1 (S2), Q10.4 (S1), Q11.1 (S2), Q11.4 (S1), Q14.1 (S2), Q14.4 (S1), Q15.1 (S2), Q15.4 (S1), Q22.1 (S2), Q22.4 (S1), Q23.1 (S2), Q23.4 (S1); also elsewhere on the board
unnamed: Q8.2 (B1), R56.1
unnamed: Q9.2 (B1), R57.1
unnamed: Q8.5 (B2), Q10.6 (D1), R56.2, R58.2
unnamed: Q10.2 (G2), Q10.3 (D2), R60.2
unnamed: C51.1, Q10.5 (G1), R62.2
unnamed: Q9.5 (B2), Q11.6 (D1), R57.2, R59.2
unnamed: Q11.2 (G2), Q11.3 (D2), R61.2
unnamed: C52.1, Q11.5 (G1), R63.2
unnamed: Q12.2 (B1), R66.1
unnamed: Q12.5 (B2), Q14.6 (D1), R66.2, R68.2
unnamed: Q13.2 (B1), R67.1
unnamed: Q13.5 (B2), Q15.6 (D1), R67.2, R69.2
unnamed: Q14.2 (G2), Q14.3 (D2), R70.2
unnamed: C53.1, Q14.5 (G1), R72.2
unnamed: Q15.2 (G2), Q15.3 (D2), R71.2
unnamed: C54.1, Q15.5 (G1), R73.2
unnamed: Q20.2 (B1), R86.1
unnamed: Q20.5 (B2), Q22.6 (D1), R86.2, R88.2
unnamed: Q21.2 (B1), R87.1
unnamed: Q21.5 (B2), Q23.6 (D1), R87.2, R89.2
unnamed: Q22.2 (G2), Q22.3 (D2), R90.2
unnamed: C57.1, Q22.5 (G1), R92.2
unnamed: Q23.2 (G2), Q23.3 (D2), R91.2
unnamed: C58.1, Q23.5 (G1), R93.2

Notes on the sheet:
Theory of operation: 10k pullup on device side of signal. 10nF is charged from power domain, turning first FET on and second FET off. Bipolar transistors turned on, connecting PROTECT_SIG to DEVICE_SIG. If DEVICE_SIG is held low, capacitor discharges, turning off bipolar transistors and disconnecti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

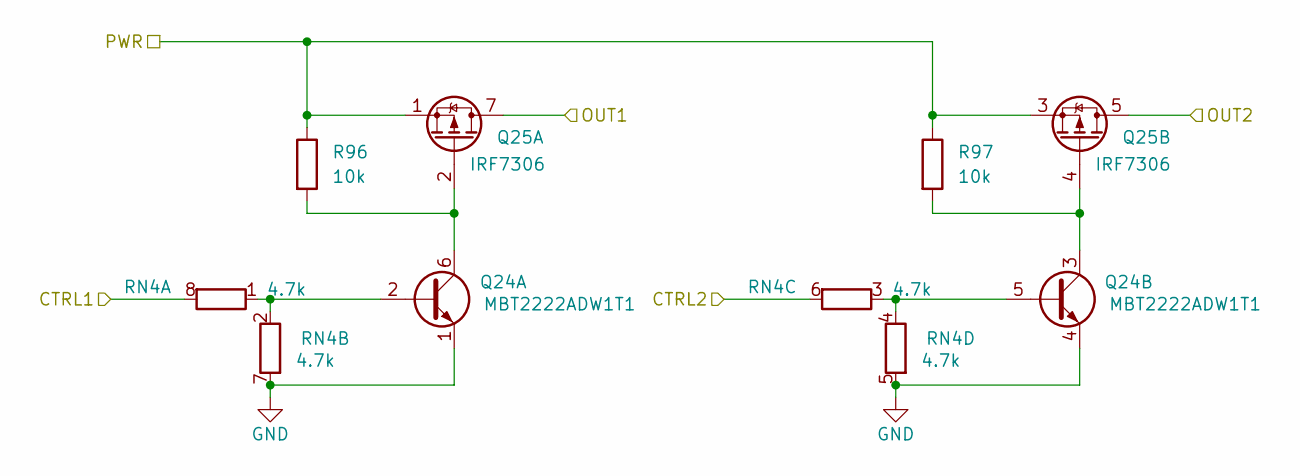
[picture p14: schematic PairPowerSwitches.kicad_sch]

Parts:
Q24: MBT2222ADW1T1; SOT-363_SC-70-6; LCSC C157366
Q25: IRF7306; SOIC-8_3.9x4.9mm_P1.27mm; LCSC C537809
R96, R97: 10k; R_0603_1608Metric
RN4: 4.7k; R_Array_Convex_4x0603

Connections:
+7.5V: Q25.1 (S1), Q25.3 (S2), R96.1, R97.1; also elsewhere on the board
/PairPowerSwitches1/OUT1: Q25.7 (D1), Q25.8 (D1); also elsewhere on the board
/PairPowerSwitches1/OUT2: Q25.5 (D2), Q25.6 (D2); also elsewhere on the board
/SW1: RN4.8 (R1.2); also elsewhere on the board
/SW2: RN4.6 (R3.2); also elsewhere on the board
GND: Q24.1 (E1), Q24.4 (E2), RN4.5 (R4.2), RN4.7 (R2.2); also elsewhere on the board
unnamed: Q24.2 (B1), RN4.1 (R1.1), RN4.2 (R2.1)
unnamed: Q24.6 (C1), Q25.2 (G1), R96.2
unnamed: Q24.5 (B2), RN4.3 (R3.1), RN4.4 (R4.1)
unnamed: Q24.3 (C2), Q25.4 (G2), R97.2

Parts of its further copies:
Q26, Q28, Q30: MBT2222ADW1T1; SOT-363_SC-70-6; LCSC C157366
Q27, Q29, Q31: IRF7306; SOIC-8_3.9x4.9mm_P1.27mm; LCSC C537809
R98, R99, R100, R101, R102, R103: 10k; R_0603_1608Metric
RN5, RN6, RN7: 4.7k; R_Array_Convex_4x0603

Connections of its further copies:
+7.5V: Q27.1 (S1), Q27.3 (S2), Q29.1 (S1), Q29.3 (S2), Q31.1 (S1), Q31.3 (S2), R98.1, R99.1, R100.1, R101.1, R102.1, R103.1; also elsewhere on the board
/PISW1: RN5.6 (R3.2); also elsewhere on the board
/PairPowerSwitches2/OUT1: Q27.7 (D1), Q27.8 (D1); also elsewhere on the board
/PairPowerSwitches2/OUT2: Q27.5 (D2), Q27.6 (D2); also elsewhere on the board
/PairPowerSwitches3/OUT1: Q29.7 (D1), Q29.8 (D1); also elsewhere on the board
/PairPowerSwitches3/OUT2: Q29.5 (D2), Q29.6 (D2); also elsewhere on the board
/PairPowerSwitches4/OUT1: Q31.7 (D1), Q31.8 (D1); also elsewhere on the board
/PairPowerSwitches4/OUT2: Q31.5 (D2), Q31.6 (D2); also elsewhere on the board
/SW3: RN5.8 (R1.2); also elsewhere on the board
/uSW1: RN6.8 (R1.2); also elsewhere on the board
/uSW2: RN6.6 (R3.2); also elsewhere on the board
/uSW3: RN7.8 (R1.2); also elsewhere on the board
/uSW4: RN7.6 (R3.2); also elsewhere on the board
GND: Q26.1 (E1), Q26.4 (E2), Q28.1 (E1), Q28.4 (E2), Q30.1 (E1), Q30.4 (E2), RN5.5 (R4.2), RN5.7 (R2.2), RN6.5 (R4.2), RN6.7 (R2.2), RN7.5 (R4.2), RN7.7 (R2.2); also elsewhere on the board
unnamed: Q26.2 (B1), RN5.1 (R1.1), RN5.2 (R2.1)
unnamed: Q26.6 (C1), Q27.2 (G1), R98.2
unnamed: Q26.5 (B2), RN5.3 (R3.1), RN5.4 (R4.1)
unnamed: Q26.3 (C2), Q27.4 (G2), R99.2
unnamed: Q28.2 (B1), RN6.1 (R1.1), RN6.2 (R2.1)
unnamed: Q28.6 (C1), Q29.2 (G1), R100.2
unnamed: Q28.5 (B2), RN6.3 (R3.1), RN6.4 (R4.1)
unnamed: Q28.3 (C2), Q29.4 (G2), R101.2
unnamed: Q30.2 (B1), RN7.1 (R1.1), RN7.2 (R2.1)
unnamed: Q30.6 (C1), Q31.2 (G1), R102.2
unnamed: Q30.5 (B2), RN7.3 (R3.1), RN7.4 (R4.1)
unnamed: Q30.3 (C2), Q31.4 (G2), R103.2

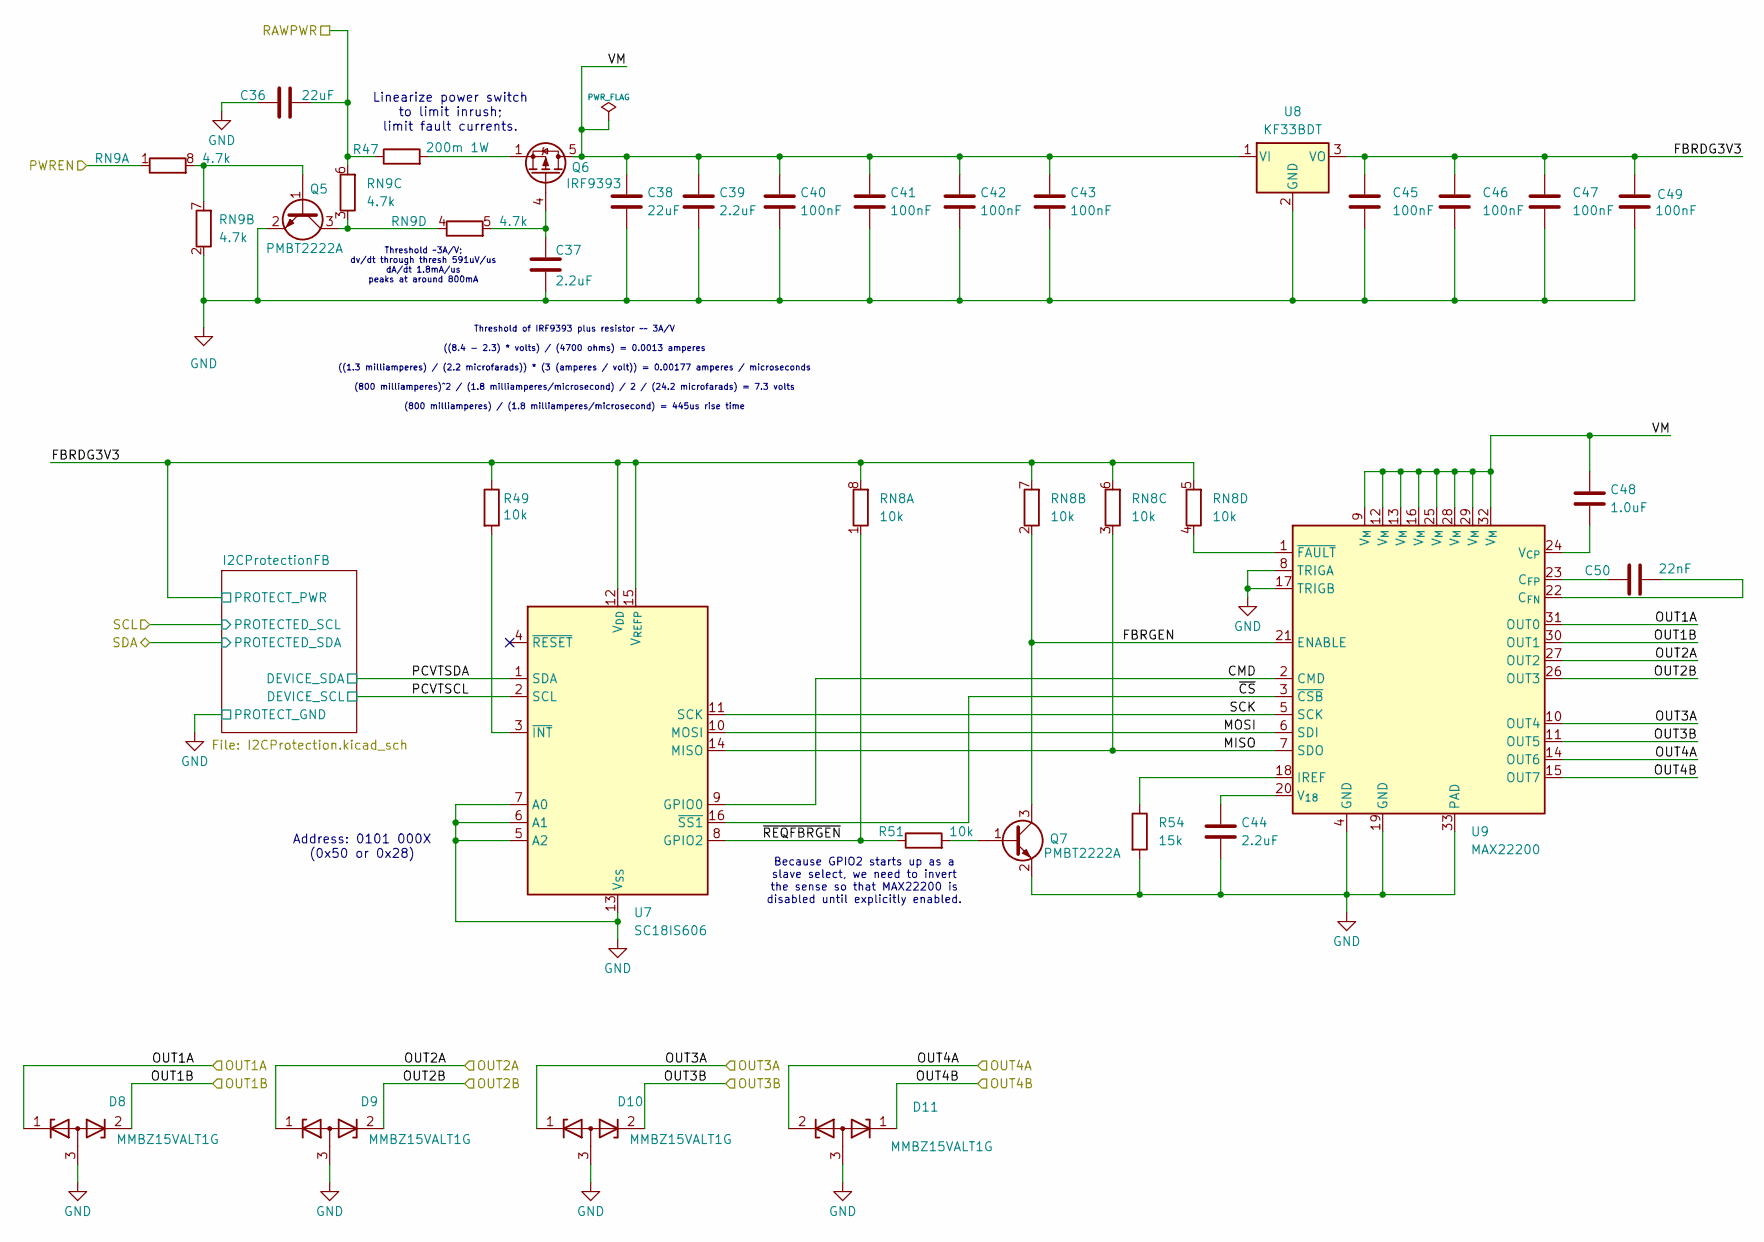
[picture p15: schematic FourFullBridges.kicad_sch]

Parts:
C36, C38: 22uF; C_0805_2012Metric
C37, C39, C44: 2.2uF; C_0603_1608Metric
C40, C41, C42, C43, C45, C46, C47, C49: 100nF; C_0603_1608Metric
C48: 1.0uF; C_0603_1608Metric
C50: 22nF; C_0603_1608Metric
D8, D9, D10, D11: MMBZ15VALT1G; SOT-23
Q5, Q7: PMBT2222A; SOT-23; LCSC C23869
Q6: IRF9393; SOIC-8_3.9x4.9mm_P1.27mm; LCSC C520642
R47: 200m 1W; R_1206_3216Metric
R49, R51: 10k; R_0603_1608Metric
R54: 15k; R_0603_1608Metric
RN8: 10k; R_Array_Convex_4x0603
RN9: 4.7k; R_Array_Convex_4x0603
U7: SC18IS606; TSSOP-16_4.4x5mm_P0.65mm
U8: KF33BDT; TO-252-2; LCSC C283274
U9: MAX22200; QFN-32-1EP_5x5mm_P0.5mm_EP3.1x3.1mm_ThermalVias

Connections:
+BATT: C36.2, R47.1, RN9.6 (R3.2); also elsewhere on the board
/FBRGPWREN: RN9.1 (R1.1); also elsewhere on the board
/FourFullBridges/CMD: U7.9 (GPIO0), U9.2 (CMD)
/FourFullBridges/FBRDG3V3: C45.1, C46.1, C47.1, C49.1, R49.1, RN8.5 (R4.2), RN8.6 (R3.2), RN8.7 (R2.2), RN8.8 (R1.2), U7.12 (V_{DD}), U7.15 (V_{REFP}), U8.3 (VO); also elsewhere on the board
/FourFullBridges/FBRGEN: Q7.3 (C), RN8.2 (R2.1), U9.21 (ENABLE)
/FourFullBridges/MISO: RN8.3 (R3.1), U7.14 (MISO), U9.7 (SDO)
/FourFullBridges/MOSI: U7.10 (MOSI), U9.6 (SDI)
/FourFullBridges/OUT1A: D8.1 (K), U9.31 (OUT0); also elsewhere on the board
/FourFullBridges/OUT1B: D8.2 (K), U9.30 (OUT1); also elsewhere on the board
/FourFullBridges/OUT2A: D9.1 (K), U9.27 (OUT2); also elsewhere on the board
/FourFullBridges/OUT2B: D9.2 (K), U9.26 (OUT3); also elsewhere on the board
/FourFullBridges/OUT3A: D10.1 (K), U9.10 (OUT4); also elsewhere on the board
/FourFullBridges/OUT3B: D10.2 (K), U9.11 (OUT5); also elsewhere on the board
/FourFullBridges/OUT4A: D11.2 (K), U9.14 (OUT6); also elsewhere on the board
/FourFullBridges/OUT4B: D11.1 (K), U9.15 (OUT7); also elsewhere on the board
/FourFullBridges/PCVTSCL: U7.2 (SCL); also elsewhere on the board
/FourFullBridges/PCVTSDA: U7.1 (SDA); also elsewhere on the board
/FourFullBridges/SCK: U7.11 (SCK), U9.5 (SCK)
/FourFullBridges/VM: C38.1, C39.1, C40.1, C41.1, C42.1, C43.1, C48.1, Q6.5 (D), Q6.6 (D), Q6.7 (D), Q6.8 (D), U8.1 (VI), U9.9 (V_{M}), U9.12 (V_{M}), U9.13 (V_{M}), U9.16 (V_{M}), U9.25 (V_{M}), U9.28 (V_{M}), U9.29 (V_{M}), U9.32 (V_{M})
/FourFullBridges/~CS: U7.16 (~SS1), U9.3 (~CSB)
/FourFullBridges/~REQFBRGEN: R51.1, RN8.1 (R1.1), U7.8 (GPIO2)
GND: C36.1, C37.2, C38.2, C39.2, C40.2, C41.2, C42.2, C43.2, C44.2, C45.2, C46.2, C47.2, C49.2, D8.3 (A), D9.3 (A), D10.3 (A), D11.3 (A), Q5.2 (E), Q7.2 (E), R54.2, RN9.2 (R2.1), U7.5 (A2), U7.6 (A1), U7.7 (A0), U7.13 (V_{SS}), U8.2 (GND), U9.4 (GND), U9.8 (TRIGA), U9.17 (TRIGB), U9.19 (GND), U9.33 (PAD); also elsewhere on the board
unnamed: Q5.1 (B), RN9.7 (R2.2), RN9.8 (R1.2)
unnamed: Q5.3 (C), RN9.3 (R3.1), RN9.4 (R4.1)
unnamed: C37.1, Q6.4 (G), RN9.5 (R4.2)
unnamed: Q6.1 (S), Q6.2 (S), Q6.3 (S), R47.2
unnamed: Q7.1 (B), R51.2
unnamed: RN8.4 (R4.1), U9.1 (~FAULT)
unnamed: R49.2, U7.3 (~INT)
unnamed: C50.2, U9.22 (C_{FN})
unnamed: C50.1, U9.23 (C_{FP})
unnamed: R54.1, U9.18 (IREF)
unnamed: C44.1, U9.20 (V_{18})
unnamed: C48.2, U9.24 (V_{CP})

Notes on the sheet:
Threshold of IRF9393 plus resistor ~~ 3A/V ((8.4 - 2.3) * volts) / (4700 ohms) = 0.0013 amperes ((1.3 milliamperes) / (2.2 microfarads)) * (3 (amperes / volt)) = 0.00177 amperes / microseconds (800 milliamperes)^2 / (1.8 milliamperes/microsecond) / 2 / (24.2 microfarads) = 7.3 volts (800 milliamper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
Linearize power switch to limit inrush; limit fault currents.
Threshold ~3A/V; dv/dt through thresh 591uV/us dA/dt 1.8mA/us peaks at around 800mA
Because GPIO2 starts up as a slave select, we need to invert the sense so that MAX22200 is disabled until explicitly enabled.
Address: 0101 000X (0x50 or 0x28)

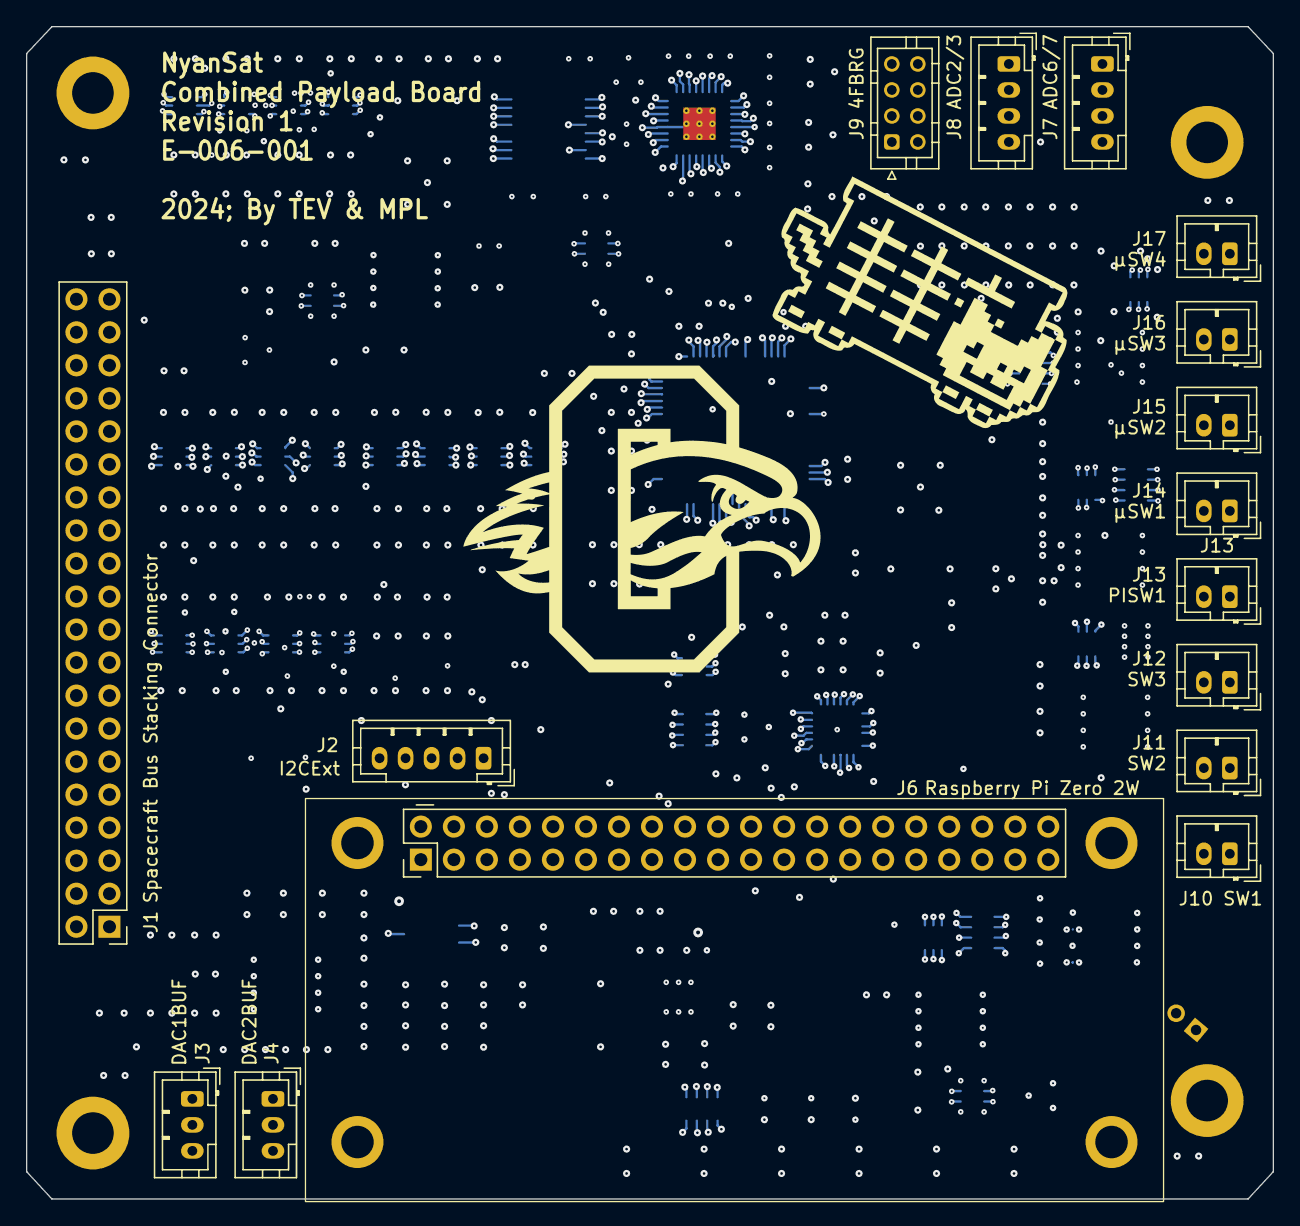
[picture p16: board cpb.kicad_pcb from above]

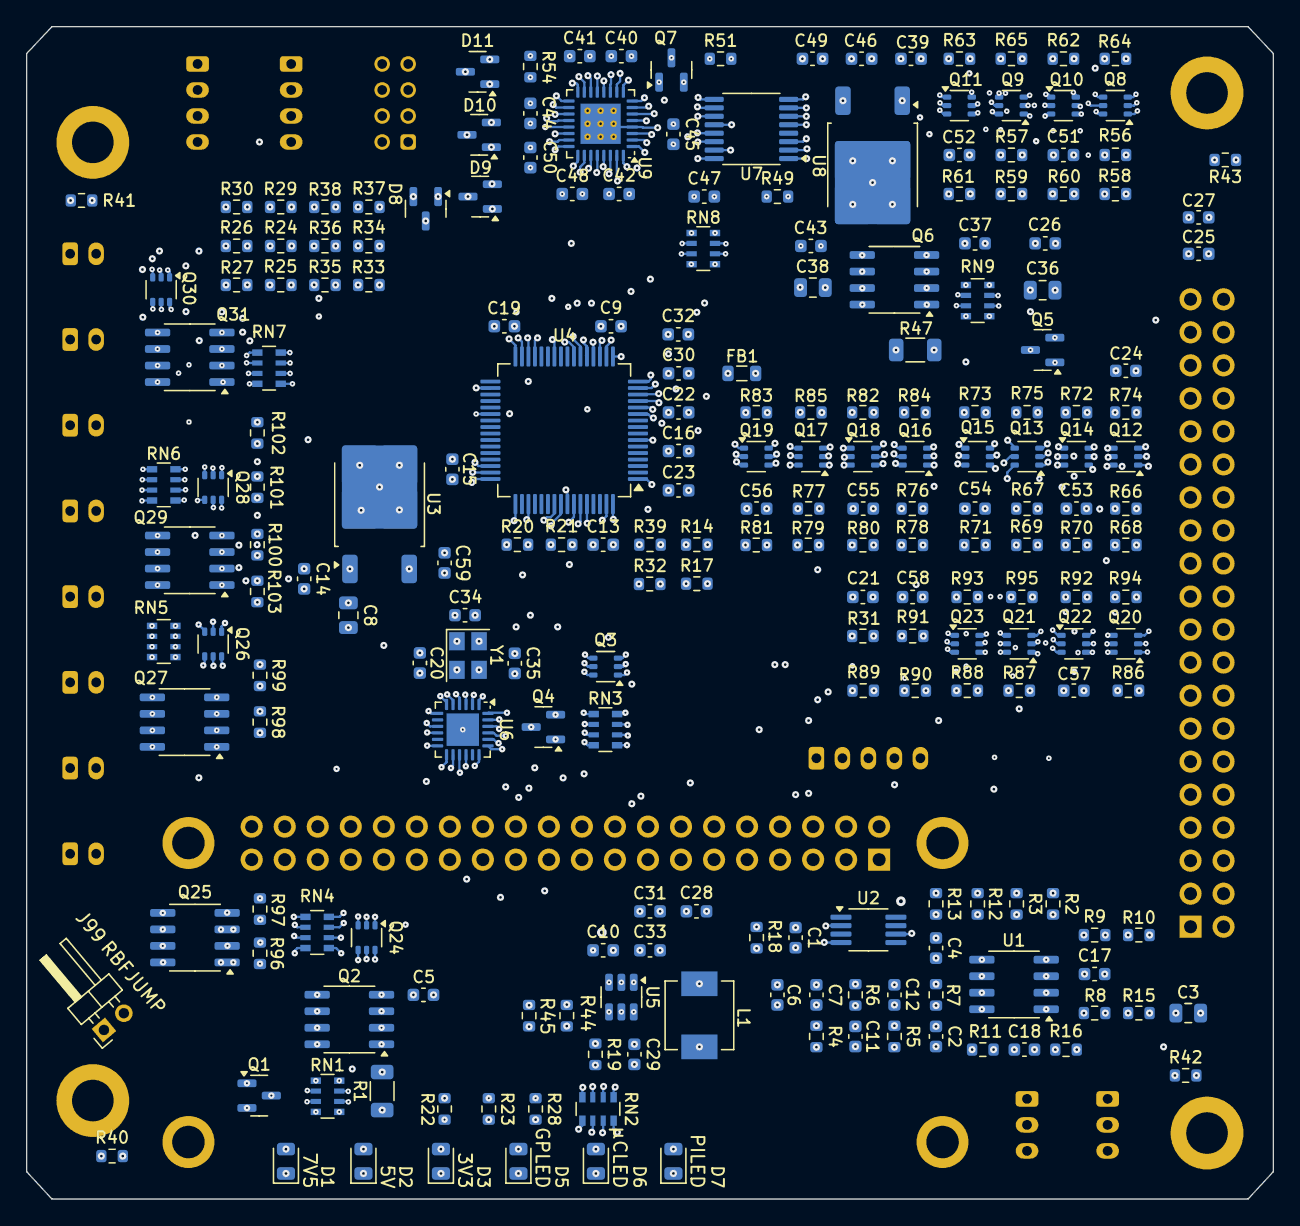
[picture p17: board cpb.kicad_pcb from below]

Board: 6 copper layers, 95.9 x 90.2 mm, 239 parts (219 on the bottom side), 178 nets.

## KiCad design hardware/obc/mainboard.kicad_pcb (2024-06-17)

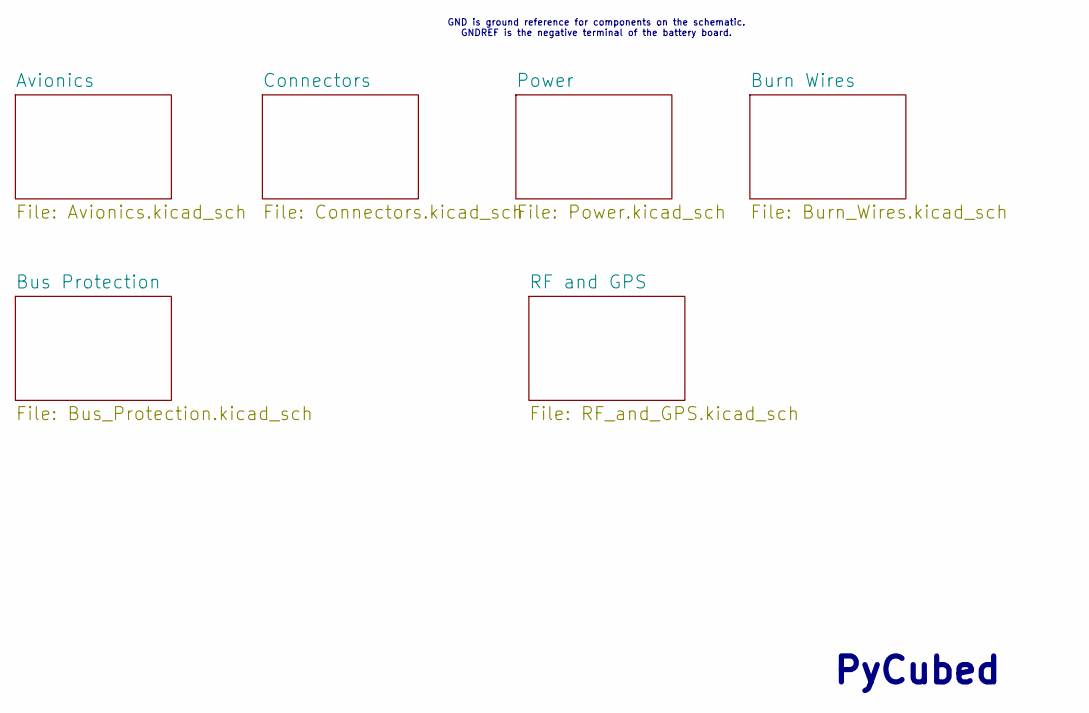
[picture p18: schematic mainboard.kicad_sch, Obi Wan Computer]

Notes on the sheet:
GND is ground reference for components on the schematic. GNDREF is the negative terminal of the battery board.
PyCubed

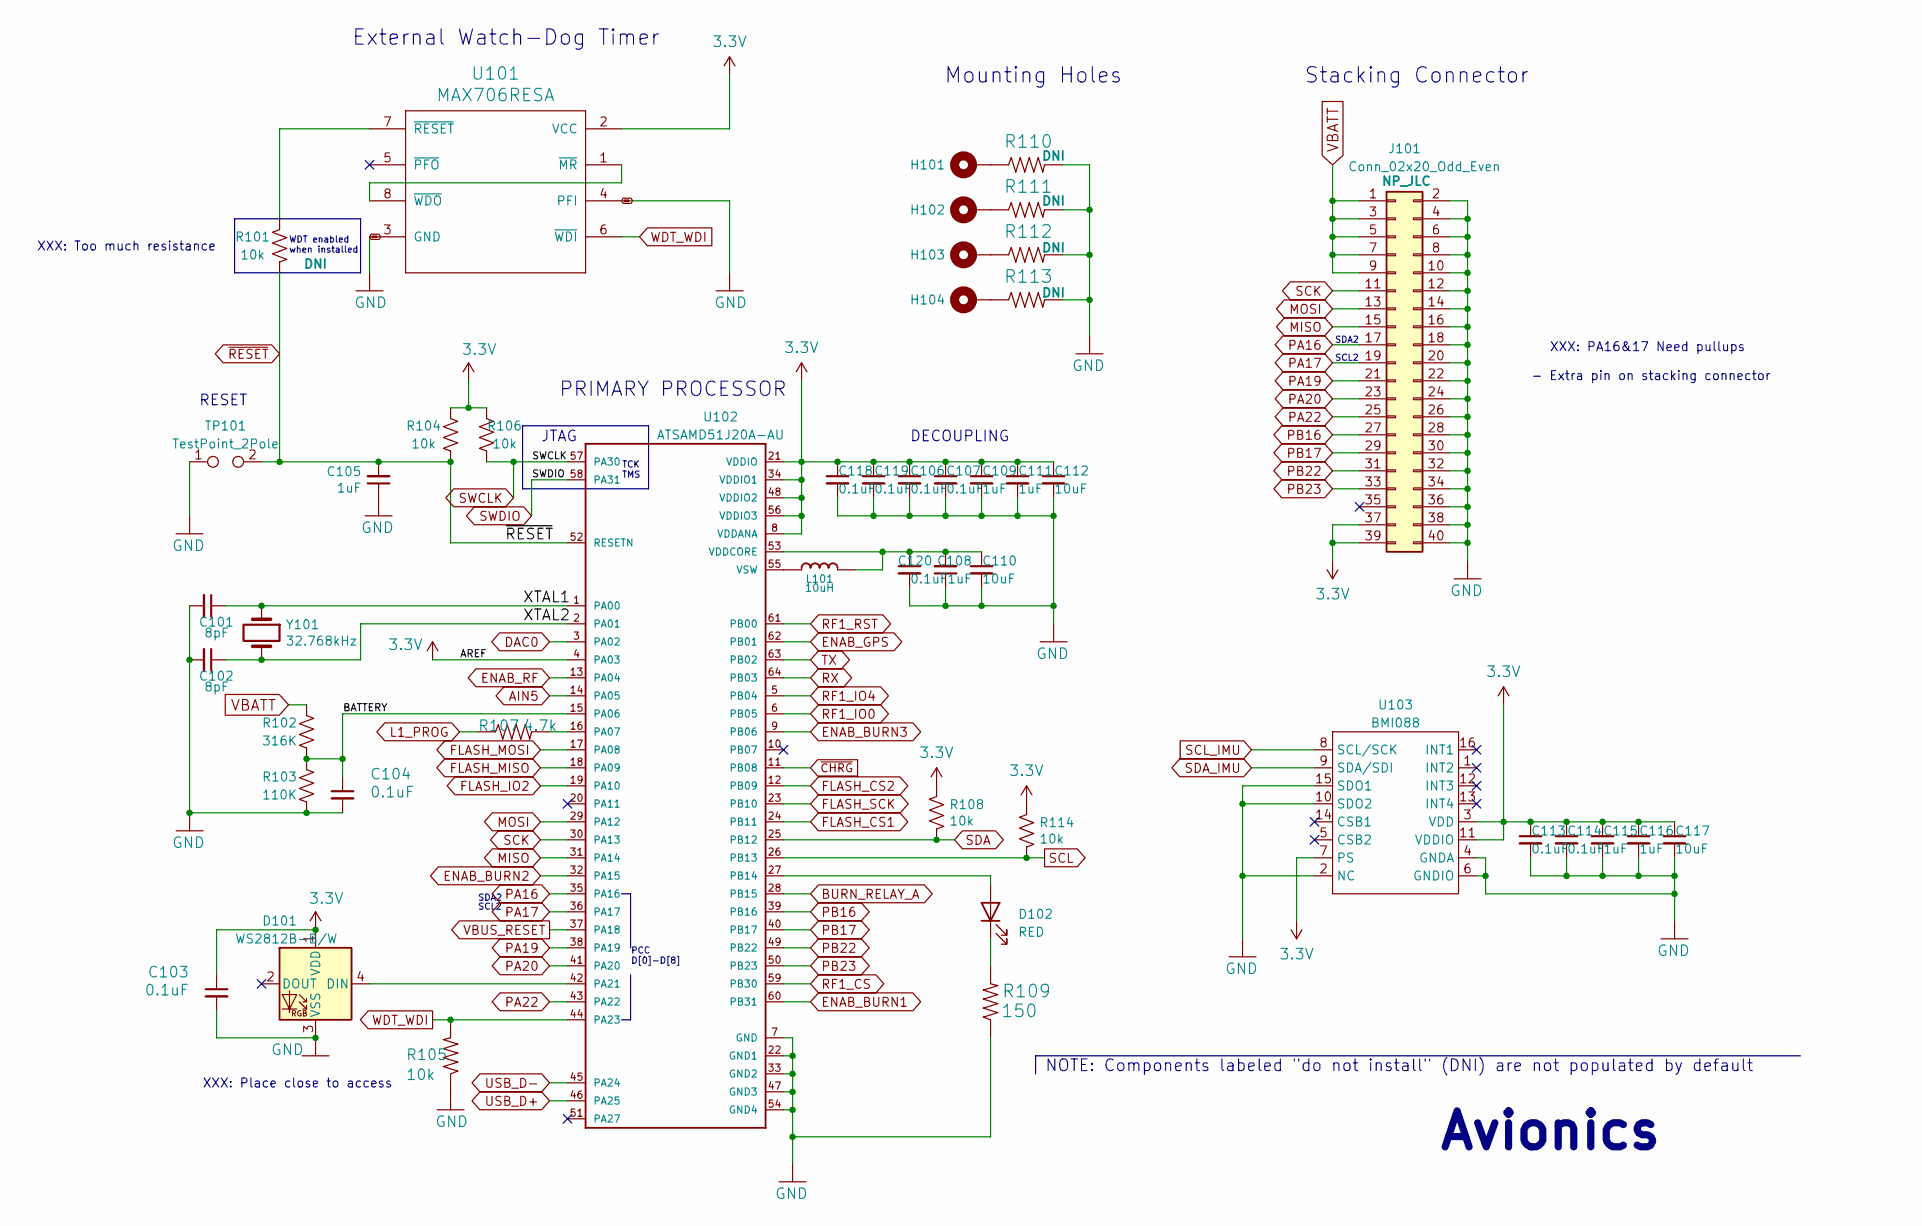
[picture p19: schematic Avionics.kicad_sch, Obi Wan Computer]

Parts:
C101, C102: 8pF; C_0603_1608Metric; Manufacturer_Part_Number CC0603JRNPO9BN8R0; LCSC C1882476
C103, C104, C106, C107, C113, C114, C118, C119, C120: 0.1uF; C_0603_1608Metric; Manufacturer_Part_Number CL10B104KB8NNNC; LCSC C1591
C105, C108, C109, C111, C115, C116: 1uF; C_0603_1608Metric; Manufacturer_Part_Number CL10B105KO8NNNC; LCSC C59782
C110, C112, C117: 10uF; C_0603_1608Metric; Manufacturer_Part_Number CL10A106MP8NNNC; LCSC C85713
D101: WS2812B-B/W; LED_WS2812B_PLCC4_5.0x5.0mm_P3.2mm; Manufacturer_Part_Number WS2812B-B/W; LCSC C114586
D102: RED; LED_0805_2012Metric; Manufacturer_Part_Number 17-215SURC/S530-A2/TR8; LCSC C142306
H101, H102, H103, H104: MountingHole_Pad; MountingHole_3.2mm_M3_DIN965_Pad
J101: Conn_02x20_Odd_Even; PinHeader_2x20_P2.54mm_Vertical
L101: 10uH; Sunlord_0805_3.0x3.0mm; Manufacturer_Part_Number SPH3012H100MT; LCSC C370419
R101, R104, R105, R106, R108, R114: 10k; R_0603_1608Metric; Manufacturer_Part_Number ERJ3GEYJ103V; LCSC C169849
R102: 316K; R_0603_1608Metric; Manufacturer_Part_Number CRCW0603316KFKEA; LCSC C844550
R103: 110K; R_0603_1608Metric; Manufacturer_Part_Number RC0603FR-07110KL; LCSC C137807
R107: 4.7k; R_0603_1608Metric; Manufacturer_Part_Number 0603WAF4701T5E; LCSC C23162
R109: 150; R_0603_1608Metric; Manufacturer_Part_Number ERJ3RBD1500V; LCSC C336847
R110, R111, R112, R113: DNI; R_0603_1608Metric
TP101: TestPoint_2Pole; TestPoint_2Pads_Pitch2.54mm_Drill0.8mm
U101: MAX706RESA; SO-8_3.9x4.9mm_P1.27mm; Manufacturer_Part_Number MAX706RESA; LCSC C28380
U102: ATSAMD51J20A-AU; TQFP-64_10x10mm_P0.5mm; Manufacturer_Part_Number ATSAMD51J20A-AU; LCSC C619371
U103: BMI088; LGA-16_4.5x3.0mm_P0.5mm; Manufacturer_Part_Number BMI088
Y101: 32.768kHz; Crystal_SMD_3215-2Pin_3.2x1.5mm; Manufacturer_Part_Number SC-32S32.768kHz20PPM7pF; LCSC C32346

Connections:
3.3V: C103.1, C106.1, C107.1, C109.1, C111.1, C112.1, C113.1, C114.1, C115.1, C116.1, C117.1, C118.1, C119.1, D101.1 (VDD), J101.37, J101.39, R104.1, R106.1, R108.1, R114.1, U101.2 (VCC), U102.4 (PA03), U102.8 (VDDANA), U102.21 (VDDIO), U102.34 (VDDIO1), U102.48 (VDDIO2), U102.56 (VDDIO3), U103.3 (VDD), U103.7 (PS), U103.11 (VDDIO); also elsewhere on the board
/Avionics/BATTERY: C104.1, R102.2, R103.2, U102.15 (PA06)
/Avionics/XTAL1: C101.1, U102.1 (PA00), Y101.1
/Avionics/XTAL2: C102.1, U102.2 (PA01), Y101.2
AIN5: U102.14 (PA05); also elsewhere on the board
BURN_RELAY_A: U102.28 (PB15); also elsewhere on the board
DAC0: U102.3 (PA02)
ENAB_BURN1: U102.60 (PB31); also elsewhere on the board
ENAB_BURN2: U102.32 (PA15); also elsewhere on the board
ENAB_BURN3: U102.9 (PB06); also elsewhere on the board
ENAB_GPS: U102.62 (PB01); also elsewhere on the board
ENAB_RF: U102.13 (PA04); also elsewhere on the board
FLASH_CS1: U102.24 (PB11); also elsewhere on the board
FLASH_CS2: U102.12 (PB09); also elsewhere on the board
FLASH_IO2: U102.19 (PA10); also elsewhere on the board
FLASH_MISO: U102.18 (PA09); also elsewhere on the board
FLASH_MOSI: U102.17 (PA08); also elsewhere on the board
FLASH_SCK: U102.23 (PB10); also elsewhere on the board
GND: C101.2, C102.2, C103.2, C104.2, C105.1, C106.2, C107.2, C108.1, C109.2, C110.2, C111.2, C112.2, C113.2, C114.2, C115.2, C116.2, C117.2, C118.2, C119.2, C120.2, D101.3 (VSS), J101.2, J101.4, J101.6, J101.8, J101.10, J101.12, J101.14, J101.16, J101.18, J101.20, J101.22, J101.24, J101.26, J101.28, J101.30, J101.32, J101.34, J101.36, J101.38, J101.40, R103.1, R105.1, R109.1, R110.2, R111.2, R112.2, R113.2, TP101.1, U101.3 (GND), U101.4 (PFI), U102.7 (GND), U102.22 (GND1), U102.33 (GND2), U102.47 (GND3), U102.54 (GND4), U103.2 (NC), U103.4 (GNDA), U103.6 (GNDIO), U103.10 (SDO2), U103.15 (SDO1); also elsewhere on the board
L1_PROG: R107.1; also elsewhere on the board
MISO: J101.15, U102.31 (PA14); also elsewhere on the board
MOSI: J101.13, U102.29 (PA12); also elsewhere on the board
unnamed: D101.4 (DIN), U102.42 (PA21)
unnamed: D102.2 (A), U102.27 (PB14)
unnamed: D102.1 (K), R109.2
unnamed: H101.1, R110.1
unnamed: H102.1, R111.1
unnamed: H103.1, R112.1
unnamed: H104.1, R113.1
unnamed: U101.1 (~MR), U101.8 (~WDO)
unnamed: R101.2, U101.7 (~RESET)
unnamed: R107.2, U102.16 (PA07)
unnamed: C108.2, C110.1, C120.1, L101.1, U102.53 (VDDCORE)
unnamed: L101.2, U102.55 (VSW)
PA16: J101.17, U102.35 (PA16)
PA17: J101.19, U102.36 (PA17)
PA19: J101.21, U102.38 (PA19)
PA20: J101.23, U102.41 (PA20)
PA22: J101.25, U102.43 (PA22)
PB16: J101.27, U102.39 (PB16)
PB17: J101.29, U102.40 (PB17)
PB22: J101.31, U102.49 (PB22)
PB23: J101.33, U102.50 (PB23)
RF1_CS: U102.59 (PB30); also elsewhere on the board
RF1_IO0: U102.6 (PB05); also elsewhere on the board
RF1_IO4: U102.5 (PB04); also elsewhere on the board
RF1_RST: U102.61 (PB00); also elsewhere on the board
RX: U102.64 (PB03); also elsewhere on the board
SCK: J101.11, U102.30 (PA13); also elsewhere on the board
SCL: R114.2, U102.26 (PB13); also elsewhere on the board
SCL_IMU: U103.8 (SCL/SCK); also elsewhere on the board
SDA: R108.2, U102.25 (PB12); also elsewhere on the board
SDA_IMU: U103.9 (SDA/SDI); also elsewhere on the board
SWCLK: R106.2, U102.57 (PA30); also elsewhere on the board
SWDIO: U102.58 (PA31); also elsewhere on the board
TX: U102.63 (PB02); also elsewhere on the board
USB_D+: U102.46 (PA25); also elsewhere on the board
USB_D-: U102.45 (PA24); also elsewhere on the board
VBATT: J101.1, J101.3, J101.5, J101.7, J101.9, R102.1; also elsewhere on the board
VBUS_RESET: U102.37 (PA18); also elsewhere on the board
WDT_WDI: R105.2, U101.6 (~WDI), U102.44 (PA23)
~CHRG: U102.11 (PB08); also elsewhere on the board
~RESET: C105.2, R101.1, R104.2, TP101.2, U102.52 (RESETN); also elsewhere on the board

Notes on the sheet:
WDT enabled when installed
Mounting Holes
NOTE: Components labeled "do not install" (DNI) are not populated by default
Avionics
XXX: PA16&17 Need pullups - Extra pin on stacking connector
XXX: Place close to access
XXX: Too much resistance
TCK TMS
RESET
SDA2
External Watch-Dog Timer
SCL2
PCC D[0]-D[8]
DECOUPLING
JTAG
PRIMARY PROCESSOR
Stacking Connector

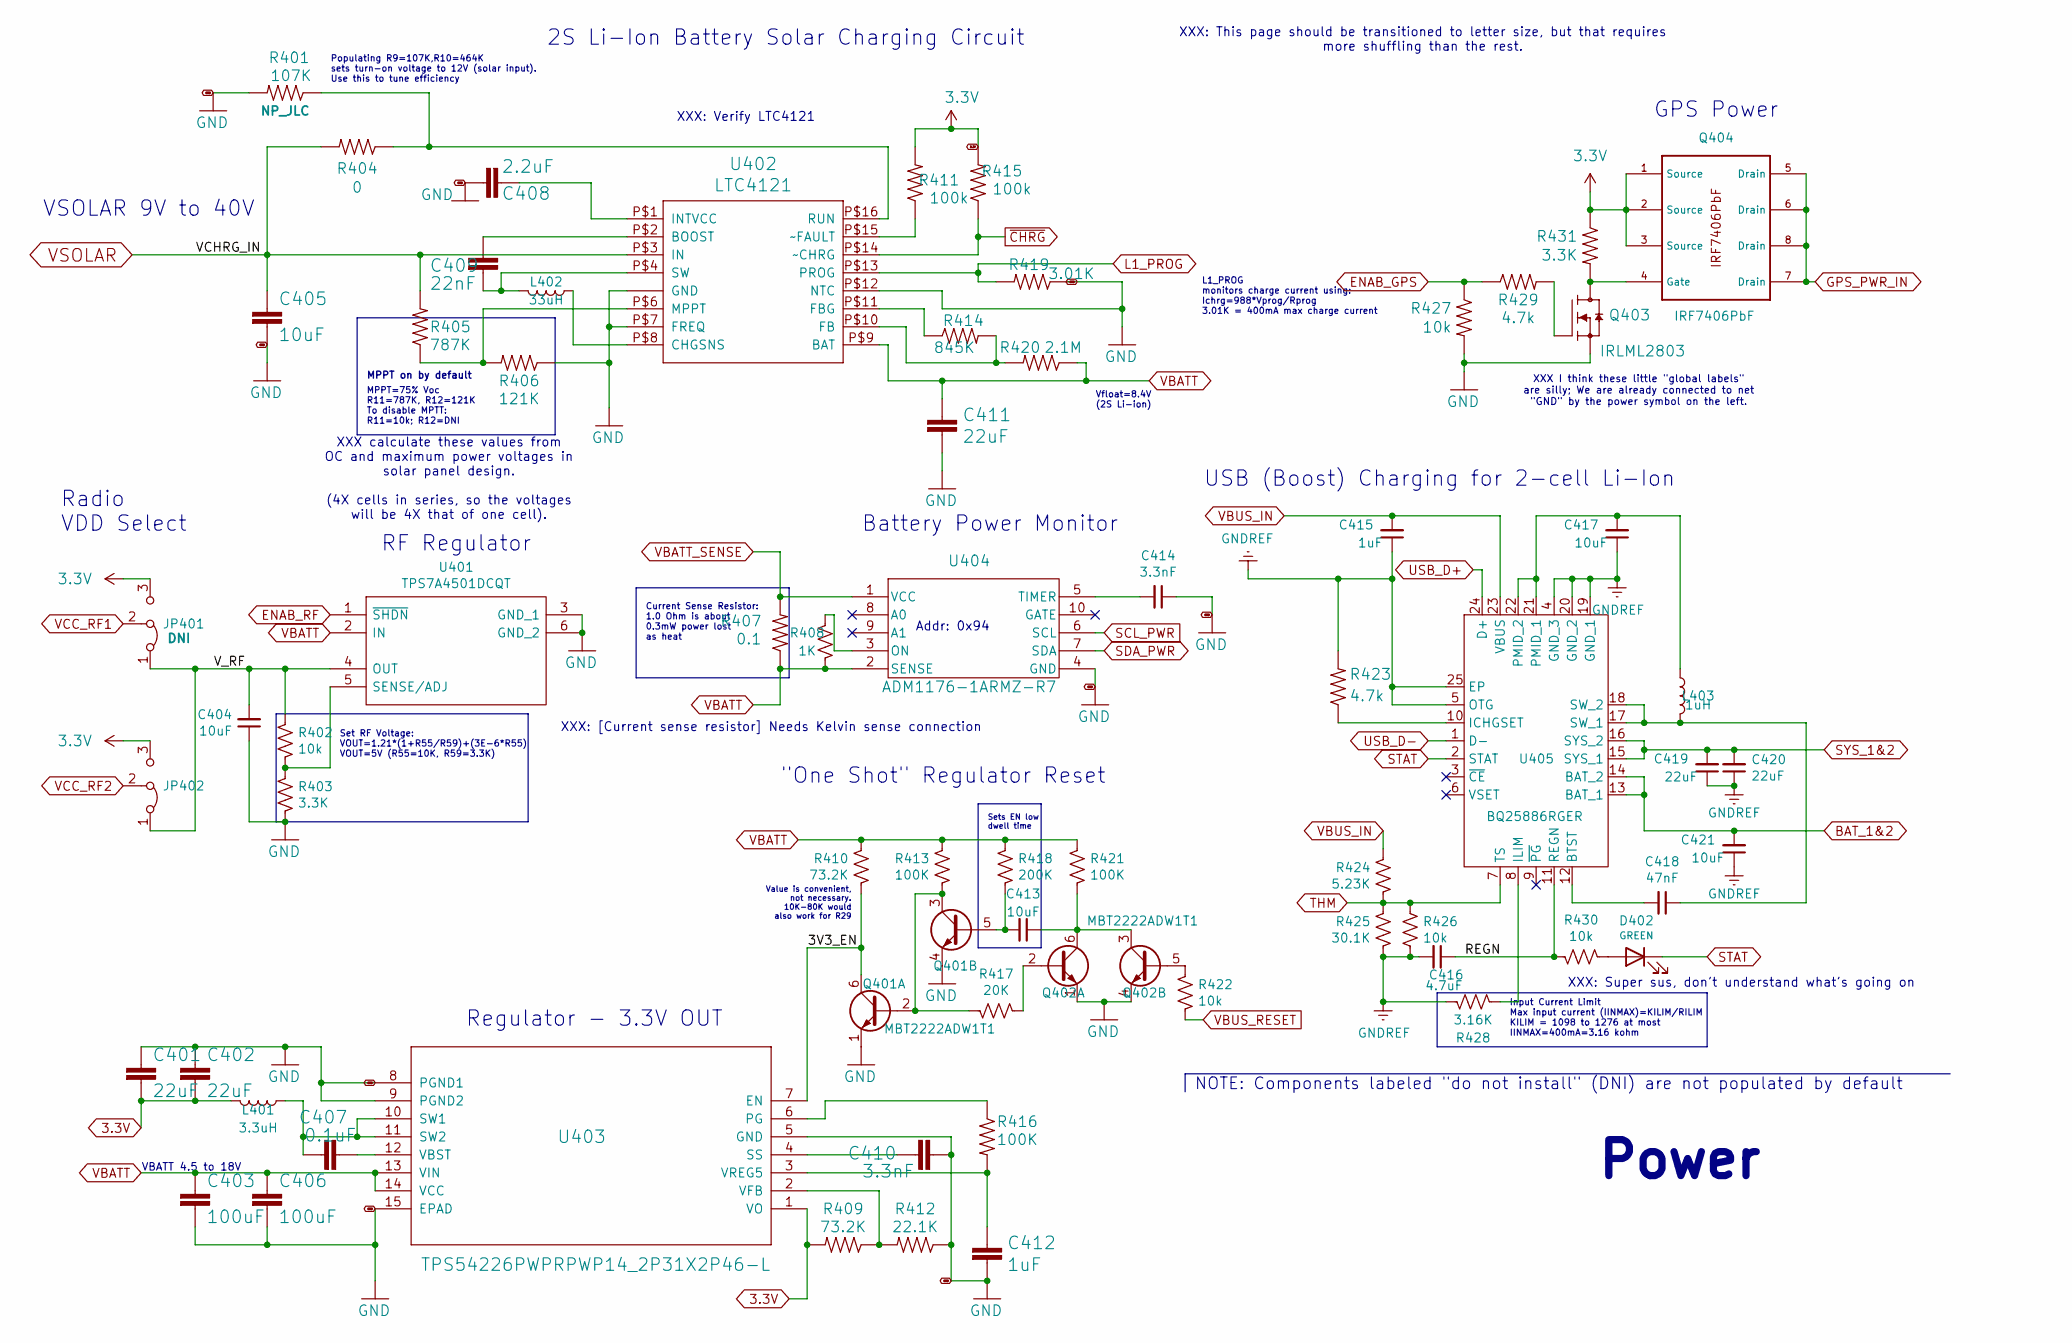
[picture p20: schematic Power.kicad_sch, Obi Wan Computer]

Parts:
C401, C402, C411, C419, C420: 22uF; C_0603_1608Metric; Manufacturer_Part_Number GRM188R61A226ME15D; LCSC C84419
C403, C406: 100uF; C_1210_3225Metric; Manufacturer_Part_Number EMK325ABJ107MM-P; LCSC C90143
C404, C405, C413, C417, C421: 10uF; C_0603_1608Metric; Manufacturer_Part_Number CL10A106MP8NNNC; LCSC C85713
C407: 0.1uF; C_0603_1608Metric; Manufacturer_Part_Number CL10B104KB8NNNC; LCSC C1591
C408: 2.2uF; C_0603_1608Metric; Manufacturer_Part_Number CL10A225KO8NNNC; LCSC C23630
C409: 22nF; C_0603_1608Metric; Manufacturer_Part_Number CL10B223KB8NNNC; LCSC C21122
C410, C414: 3.3nF; C_0603_1608Metric; Manufacturer_Part_Number CL10B332KB8NNNC; LCSC C1613
C412, C415: 1uF; C_0603_1608Metric; Manufacturer_Part_Number CL10B105KO8NNNC; LCSC C59782
C416: 4.7uF; C_0603_1608Metric; Manufacturer_Part_Number CL10A475KP8NNNC; LCSC C1705
C418: 47nF; C_0603_1608Metric; Manufacturer_Part_Number CL10B473KB8NNNC; LCSC C1622
D402: GREEN; LED_0805_2012Metric; Manufacturer_Part_Number KT-0805G; LCSC C2297
JP401, JP402: Jumper_3_Bridged12; SolderJumper-3_P1.3mm_Bridged12_RoundedPad1.0x1.5mm
L401: 3.3uH; TDK_1008_2.9x2.0mm; Manufacturer_Part_Number TFM252012ALMA3R3MTAA; LCSC C404805
L402: 33uH; TDK_1008_4.9x5.5mm; Manufacturer_Part_Number VLCF5024T-330MR50-2; LCSC C2046704
L403: 1uH; L_1008_2520Metric; Manufacturer_Part_Number DFE2HCAH1R0MJ0L; LCSC C5247968
Q401, Q402: MBT2222ADW1T1; SOT-363_SC-70-6; Manufacturer_Part_Number MBT2222ADW1T1G; LCSC C157366
Q403: IRLML2803; SOT-23; Manufacturer_Part_Number IRLML2803TRPBF; LCSC C2590
Q404: IRF7406PbF; SO-8_3.9x4.9mm_P1.27mm; Manufacturer_Part_Number IRF7406TRPBF; LCSC C169769
R401: 107K; R_0603_1608Metric
R402, R422, R426, R427, R430: 10k; R_0603_1608Metric; Manufacturer_Part_Number ERJ3GEYJ103V; LCSC C169849
R403, R431: 3.3K; R_0603_1608Metric; Manufacturer_Part_Number CRCW06033K30JNEA; LCSC C844782
R404: 0; R_0603_1608Metric; Manufacturer_Part_Number MCT06030Z0000ZP500; LCSC C2654002
R405: 787K; R_0603_1608Metric; Manufacturer_Part_Number RC0603FR-07787KL; LCSC C246008
R406: 121K; R_0603_1608Metric; Manufacturer_Part_Number RT0603BRD07121KL; LCSC C861095
R407: 0.1; R_2512_6332Metric; LCSC C165698
R408: 1K; R_0603_1608Metric; Manufacturer_Part_Number CRCW06031K00FKEAC; LCSC C844746
R409, R410: 73.2K; R_0603_1608Metric; Manufacturer_Part_Number CRCW060373K2FKEA; LCSC C843966
R411, R415: 100k; R_0603_1608Metric; Manufacturer_Part_Number CRCW0603100KFKEC; LCSC C5369222
R412: 22.1K; R_0603_1608Metric; Manufacturer_Part_Number AF0603FR-0722K1L; LCSC C2838732
R413, R416, R421: 100K; R_0603_1608Metric; Manufacturer_Part_Number CRCW0603100KFKEC; LCSC C5369222
R414: 845K; R_0603_1608Metric; Manufacturer_Part_Number CRCW0603845KFKEA; LCSC C2091473
R417: 20K; R_0603_1608Metric; Manufacturer_Part_Number CRCW060320K0FKEC; LCSC C2076573
R418: 200K; R_0603_1608Metric; Manufacturer_Part_Number ERA3AEB204V; LCSC C473261
R419: 3.01K; R_0603_1608Metric; Manufacturer_Part_Number TNPW06033K01BEEA; LCSC C2075334
R420: 2.1M; R_0603_1608Metric; Manufacturer_Part_Number CRCW06032M10FKEA; LCSC C2085910
R423, R429: 4.7k; R_0603_1608Metric; Manufacturer_Part_Number 0603WAF4701T5E; LCSC C23162
R424: 5.23K; R_0603_1608Metric; Manufacturer_Part_Number AC0603FR-075K23L; LCSC C227977
R425: 30.1K; R_0603_1608Metric; Manufacturer_Part_Number RC0603FR-0730K1L; LCSC C137745
R428: 3.16K; R_0603_1608Metric; Manufacturer_Part_Number RC0603FR-073K16L; LCSC C185333
U401: TPS7A4501DCQT; SOT-223-6; Manufacturer_Part_Number TPS7A4501DCQT; LCSC C2869558
U402: LTC4121; QFN-16-PAD; Manufacturer_Part_Number LTC4121EUD; LCSC C687336
U403: TPS54226PWPRPWP14_2P31X2P46-L; HTSSOP-14-1EP_4.4x5mm_P0.65mm_EP3.4x5mm_Mask3x3.1mm; Manufacturer_Part_Number TPS54226PWPR; LCSC C72066
U404: ADM1176-1ARMZ-R7; Manufacturer_Part_Number ADM1176-1ARMZ-R7; LCSC C657860
U405: BQ25886RGER; QFN50P400X400X100-25N-D; Manufacturer_Part_Number BQ25886RGER; LCSC C2765094

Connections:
3.3V: C401.2, C402.2, JP401.3 (B), JP402.3 (B), L401.2, Q404.1 (Source), Q404.2 (Source), Q404.3 (Source), R409.2, R411.2, R415.2, R431.1, U403.1 (VO); also elsewhere on the board
/Power/3V3_EN: Q401.6 (C1), R410.2, U403.7 (EN)
/Power/REGN: C416.1, R430.2, U405.11 (REGN)
/Power/V_RF: C404.2, JP401.1 (A), JP402.1 (A), R402.1, U401.4 (OUT)
BAT_1&2: C421.2, U405.13 (BAT_1), U405.14 (BAT_2); also elsewhere on the board
ENAB_GPS: R427.1, R429.1; also elsewhere on the board
ENAB_RF: U401.1 (~SHDN); also elsewhere on the board
GND: C401.1, C402.1, C403.2, C404.1, C405.2, C406.2, C408.2, C410.2, C411.2, C412.2, C414.1, Q401.1 (E1), Q401.4 (E2), Q402.1 (E1), Q402.4 (E2), Q403.2 (S), R401.2, R403.2, R406.1, R412.1, R419.1, R427.2, U401.3 (GND_1), U401.6 (GND_2), U402.P$5 (GND), U402.P$7 (FREQ), U402.P$12 (NTC), U402.P$17 (GND), U403.5 (GND), U403.8 (PGND1), U403.9 (PGND2), U403.15 (EPAD), U404.4 (GND); also elsewhere on the board
GNDREF: C415.1, C416.2, C417.1, C419.1, C420.1, C421.1, R423.2, R425.1, R426.1, R428.1, U405.4 (GND_3), U405.5 (OTG), U405.19 (GND_1), U405.20 (GND_2), U405.25 (EP); also elsewhere on the board
GPS_PWR_IN: Q404.5 (Drain), Q404.6 (Drain), Q404.7 (Drain), Q404.8 (Drain); also elsewhere on the board
L1_PROG: R419.2, U402.P$13 (PROG); also elsewhere on the board
unnamed: D402.2 (A), R430.1
unnamed: Q401.2 (B1), Q401.3 (C2), R413.2, R417.2
unnamed: C413.2, Q401.5 (B2), R418.2
unnamed: Q402.2 (B1), R417.1
unnamed: C413.1, Q402.3 (C2), Q402.6 (C1), R421.2
unnamed: Q402.5 (B2), R422.1
unnamed: Q403.3 (D), Q404.4 (Gate), R431.2
unnamed: Q403.1 (G), R429.2
unnamed: R402.2, R403.1, U401.5 (SENSE/ADJ)
unnamed: C409.1, U402.P$2 (BOOST)
unnamed: L402.1, U402.P$8 (CHGSNS)
unnamed: R414.2, R420.2, U402.P$10 (FB)
unnamed: R414.1, U402.P$11 (FBG)
unnamed: C408.1, U402.P$1 (INTVCC)
unnamed: R405.1, R406.2, U402.P$6 (MPPT)
unnamed: R401.1, R404.1, U402.P$16 (RUN)
unnamed: C409.2, L402.2, U402.P$4 (SW)
unnamed: R411.1, U402.P$15 (~FAULT)
unnamed: R416.1, U403.6 (PG)
unnamed: C410.1, U403.4 (SS)
unnamed: C407.1, L401.1, U403.10 (SW1), U403.11 (SW2)
unnamed: C407.2, U403.12 (VBST)
unnamed: R409.1, R412.2, U403.2 (VFB)
unnamed: C412.1, R416.2, U403.3 (VREG5)
unnamed: R408.2, U404.3 (ON)
unnamed: C414.2, U404.5 (TIMER)
unnamed: C418.2, U405.12 (BTST)
unnamed: R423.1, U405.10 (ICHGSET)
unnamed: R428.2, U405.8 (ILIM)
unnamed: C417.2, L403.1, U405.21 (PMID_1), U405.22 (PMID_2)
unnamed: C418.1, L403.2, U405.17 (SW_1), U405.18 (SW_2)
SCL_PWR: U404.6 (SCL); also elsewhere on the board
SDA_PWR: U404.7 (SDA); also elsewhere on the board
STAT: D402.1 (K), U405.2 (STAT)
SYS_1&2: C419.2, C420.2, U405.15 (SYS_1), U405.16 (SYS_2); also elsewhere on the board
THM: R424.2, R425.2, R426.2, U405.7 (TS)
USB_D+: U405.24 (D+); also elsewhere on the board
USB_D-: U405.1 (D-); also elsewhere on the board
VBATT: C403.1, C406.1, C411.1, R407.1, R408.1, R410.1, R413.1, R418.1, R420.1, R421.1, U401.2 (IN), U402.P$9 (BAT), U403.13 (VIN), U403.14 (VCC), U404.2 (SENSE); also elsewhere on the board
VBATT_SENSE: R407.2, U404.1 (VCC); also elsewhere on the board
VBUS_IN: C415.2, R424.1, U405.23 (VBUS); also elsewhere on the board
VBUS_RESET: R422.2; also elsewhere on the board
VCC_RF1: JP401.2 (C); also elsewhere on the board
VCC_RF2: JP402.2 (C)
VSOLAR: C405.1, R404.2, R405.2, U402.P$3 (IN); also elsewhere on the board
~CHRG: R415.1, U402.P$14 (~CHRG); also elsewhere on the board

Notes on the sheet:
Set RF Voltage: VOUT=1.21*(1+R55/R59)+(3E-6*R55) VOUT=5V (R55=10K, R59=3.3K)
MPPT on by default
Sets EN low dwell time
XXX: Super sus, don't understand what's going on
Value is convenient, not necessary. 10K-80K would also work for R29
VBATT 4.5 to 18V
Regulator - 3.3V OUT
Radio VDD Select
Populating R9=107K,R10=464K sets turn-on voltage to 12V (solar input). Use this to tune efficiency
XXX: This page should be transitioned to letter size, but that requires more shuffling than the rest.
RF Regulator
L1_PROG monitors charge current using: Ichrg=988*Vprog/Rprog 3.01K = 400mA max charge current
XXX: Verify LTC4121
XXX calculate these values from OC and maximum power voltages in solar panel design. (4X cells in series, so the voltages will be 4X that of one cell).
VSOLAR 9V to 40V
GPS Power
USB (Boost) Charging for 2-cell Li-Ion
Input Current Limit Max input current (IINMAX)=KILIM/RILIM KILIM = 1098 to 1276 at most IINMAX=400mA=3.16 kohm
NOTE: Components labeled "do not install" (DNI) are not populated by default
Battery Power Monitor
Power
Addr: 0x94
2S Li-Ion Battery Solar Charging Circuit
XXX I think these little "global labels" are silly; We are already connected to net "GND" by the power symbol on the left.
Vfloat=8.4V (2S Li-ion)
XXX: [Current sense resistor] Needs Kelvin sense connection
MPPT=75% Voc R11=787K, R12=121K To disable MPTT: R11=10k; R12=DNI
Current Sense Resistor: 1.0 Ohm is about 0.3mW power lost as heat
"One Shot" Regulator Reset

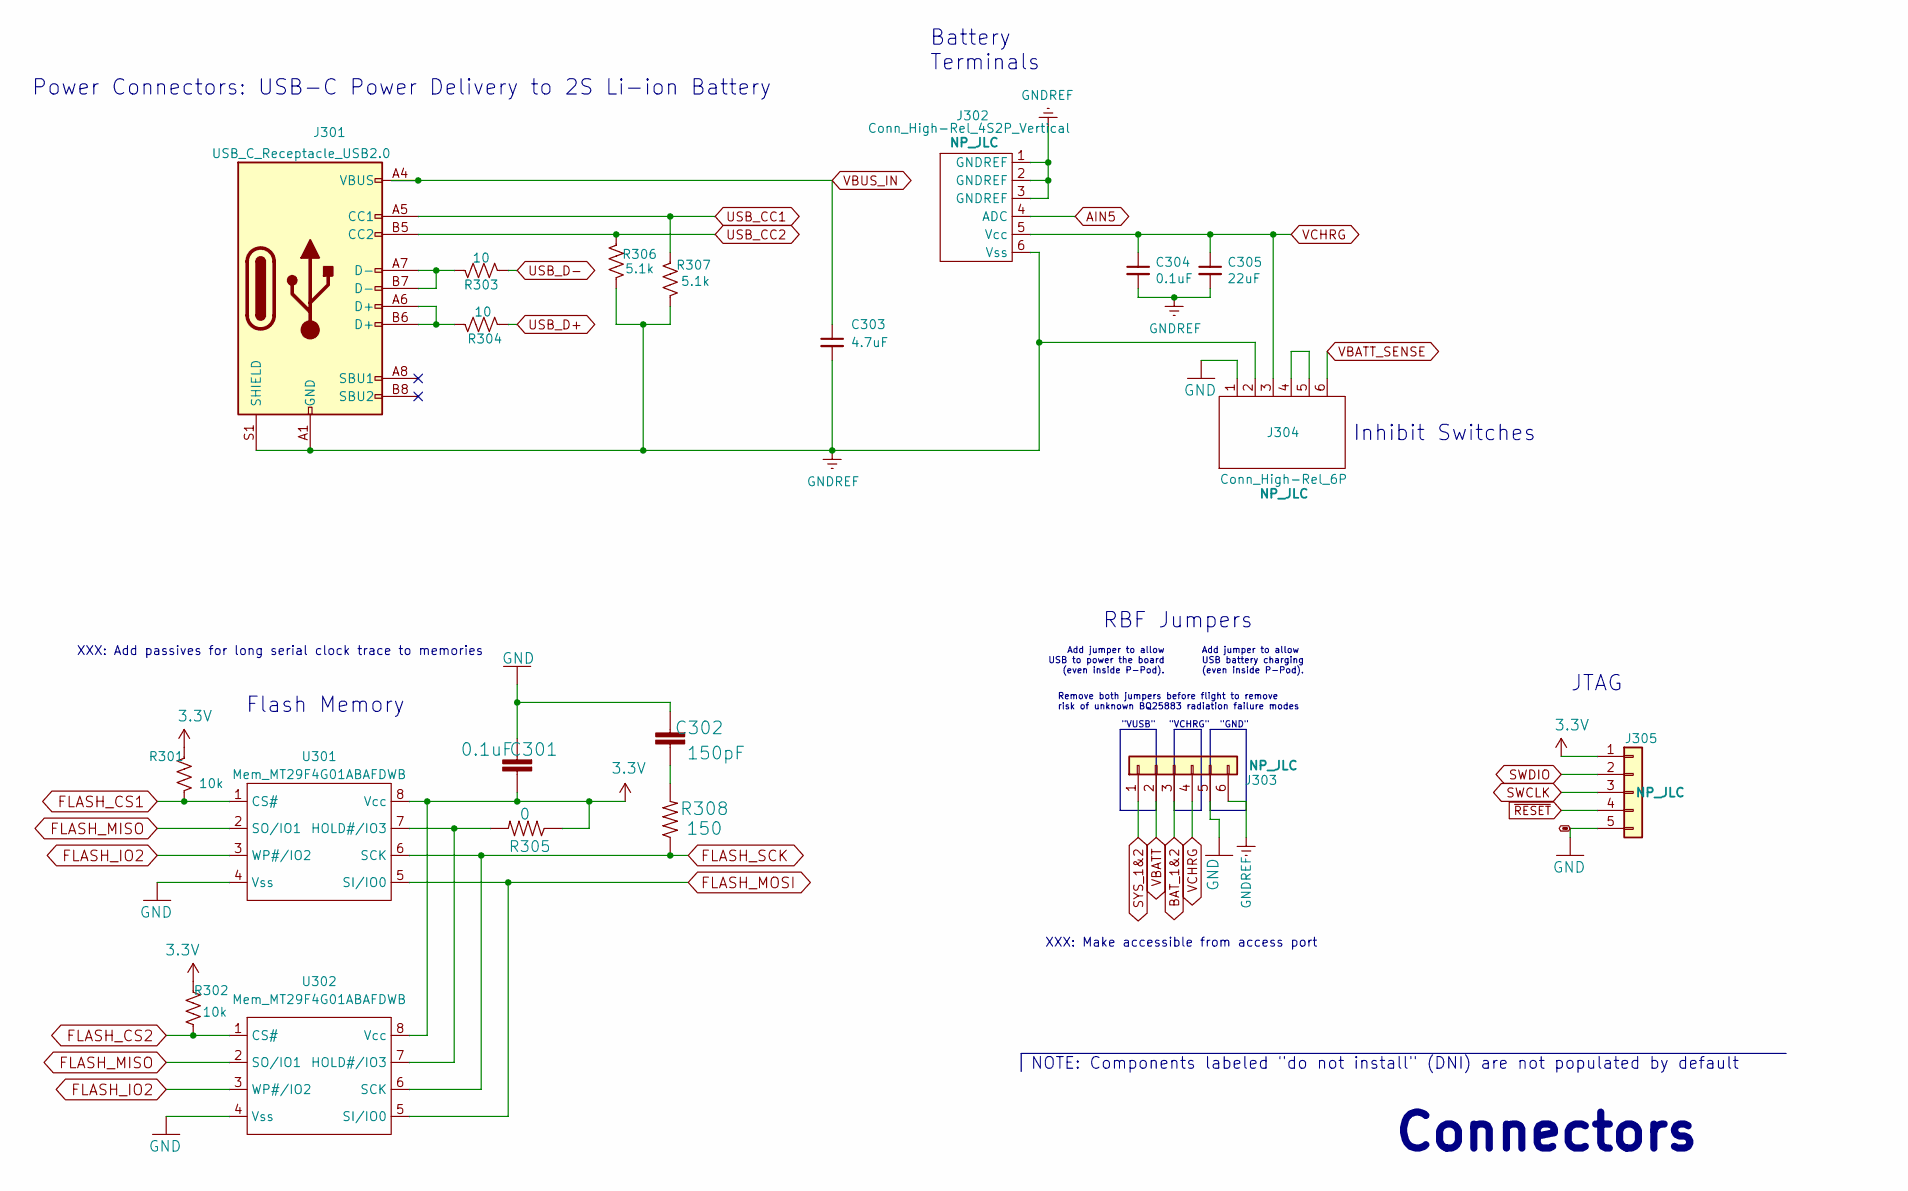
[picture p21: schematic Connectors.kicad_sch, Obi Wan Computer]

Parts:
C301, C304: 0.1uF; C_0603_1608Metric; Manufacturer_Part_Number CL10B104KB8NNNC; LCSC C1591
C302: 150pF; C_0603_1608Metric; Manufacturer_Part_Number CC0603JRNPO9BN151; LCSC C107038
C303: 4.7uF; C_0603_1608Metric; Manufacturer_Part_Number CL10A475KP8NNNC; LCSC C1705
C305: 22uF; C_0603_1608Metric; Manufacturer_Part_Number GRM188R61A226ME15D; LCSC C84419
J301: USB_C_Receptacle_USB2.0; USB_C_Receptacle_G-Switch_GT-USB-7010ASV; Manufacturer_Part_Number GT-USB-7010ASV; LCSC C2988369
J302: Conn_High-Rel_4S2P_Vertical; Harwin_G125-FV104F3-02AB000P_P1.25mm_Vertical; Manufacturer_Part_Number G125-FV104F3-02AB000P
J303: Conn_01x06; PinHeader_1x06_P2.54mm_Horizontal
J304: Conn_High-Rel_6P; MMCX-6_UMPT-06-01-L-RA-WT-TR_P2.0mm; Manufacturer_Part_Number UMPT-06-01-L-RA-WT-TR
J305: Conn_01x05; PinHeader_1x05_P2.54mm_Vertical
R301, R302: 10k; R_0603_1608Metric; Manufacturer_Part_Number ERJ3GEYJ103V; LCSC C169849
R303, R304: 10; R_0603_1608Metric; Manufacturer_Part_Number AC0603FR-0710RL; LCSC C138286
R305: 0; R_0603_1608Metric; Manufacturer_Part_Number MCT06030Z0000ZP500; LCSC C2654002
R306, R307: 5.1k; R_0603_1608Metric; Manufacturer_Part_Number RC0603FR-075K1L; LCSC C105580
R308: 150; R_0603_1608Metric; Manufacturer_Part_Number ERJ3RBD1500V; LCSC C336847
U301, U302: Mem_MT29F4G01ABAFDWB; UPDFN-8_8.0x6.0mm_P1.27mm; Manufacturer_Part_Number MT29F4G01ABAFDWB-IT:F; LCSC C2909506

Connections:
3.3V: C301.1, J305.1, R301.2, R302.2, R305.1, U301.8 (Vcc), U302.8 (Vcc); also elsewhere on the board
AIN5: J302.4 (ADC); also elsewhere on the board
BAT_1&2: J303.3; also elsewhere on the board
FLASH_CS1: R301.1, U301.1 (CS#); also elsewhere on the board
FLASH_CS2: R302.1, U302.1 (CS#); also elsewhere on the board
FLASH_IO2: U301.3 (WP#/IO2), U302.3 (WP#/IO2); also elsewhere on the board
FLASH_MISO: U301.2 (SO/IO1), U302.2 (SO/IO1); also elsewhere on the board
FLASH_MOSI: U301.5 (SI/IO0), U302.5 (SI/IO0); also elsewhere on the board
FLASH_SCK: R308.1, U301.6 (SCK), U302.6 (SCK); also elsewhere on the board
GND: C301.2, C302.2, J303.5, J304.1, J305.5, U301.4 (Vss), U302.4 (Vss); also elsewhere on the board
GNDREF: C303.2, C304.2, C305.2, J301.A1 (GND), J301.A12 (GND), J301.B1 (GND), J301.B12 (GND), J301.S1 (SHIELD), J302.1 (GNDREF), J302.2 (GNDREF), J302.3 (GNDREF), J302.6 (Vss), J303.6, J304.2, R306.1, R307.1; also elsewhere on the board
unnamed: C302.1, R308.2
unnamed: J301.A6 (D+), J301.B6 (D+), R304.2
unnamed: J301.A7 (D-), J301.B7 (D-), R303.2
unnamed: J304.4, J304.5
unnamed: R305.2, U301.7 (HOLD#/IO3), U302.7 (HOLD#/IO3)
SWCLK: J305.3; also elsewhere on the board
SWDIO: J305.2; also elsewhere on the board
SYS_1&2: J303.1; also elsewhere on the board
USB_CC1: J301.A5 (CC1), R307.2
USB_CC2: J301.B5 (CC2), R306.2
USB_D+: R304.1; also elsewhere on the board
USB_D-: R303.1; also elsewhere on the board
VBATT: J303.2; also elsewhere on the board
VBATT_SENSE: J304.6; also elsewhere on the board
VBUS_IN: C303.1, J301.A4 (VBUS), J301.A9 (VBUS), J301.B4 (VBUS), J301.B9 (VBUS); also elsewhere on the board
VCHRG: C304.1, C305.1, J302.5 (Vcc), J303.4, J304.3
~RESET: J305.4; also elsewhere on the board

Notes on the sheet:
NOTE: Components labeled "do not install" (DNI) are not populated by default
XXX: Add passives for long serial clock trace to memories
Add jumper to allow USB battery charging (even inside P-Pod).
Remove both jumpers before flight to remove risk of unknown BQ25883 radiation failure modes
Connectors
Flash Memory
Battery Terminals
"VCHRG"
XXX: Make accessible from access port
RBF Jumpers
Power Connectors: USB-C Power Delivery to 2S Li-ion Battery
"GND"
Inhibit Switches
Add jumper to allow USB to power the board (even inside P-Pod).
"VUSB"
JTAG

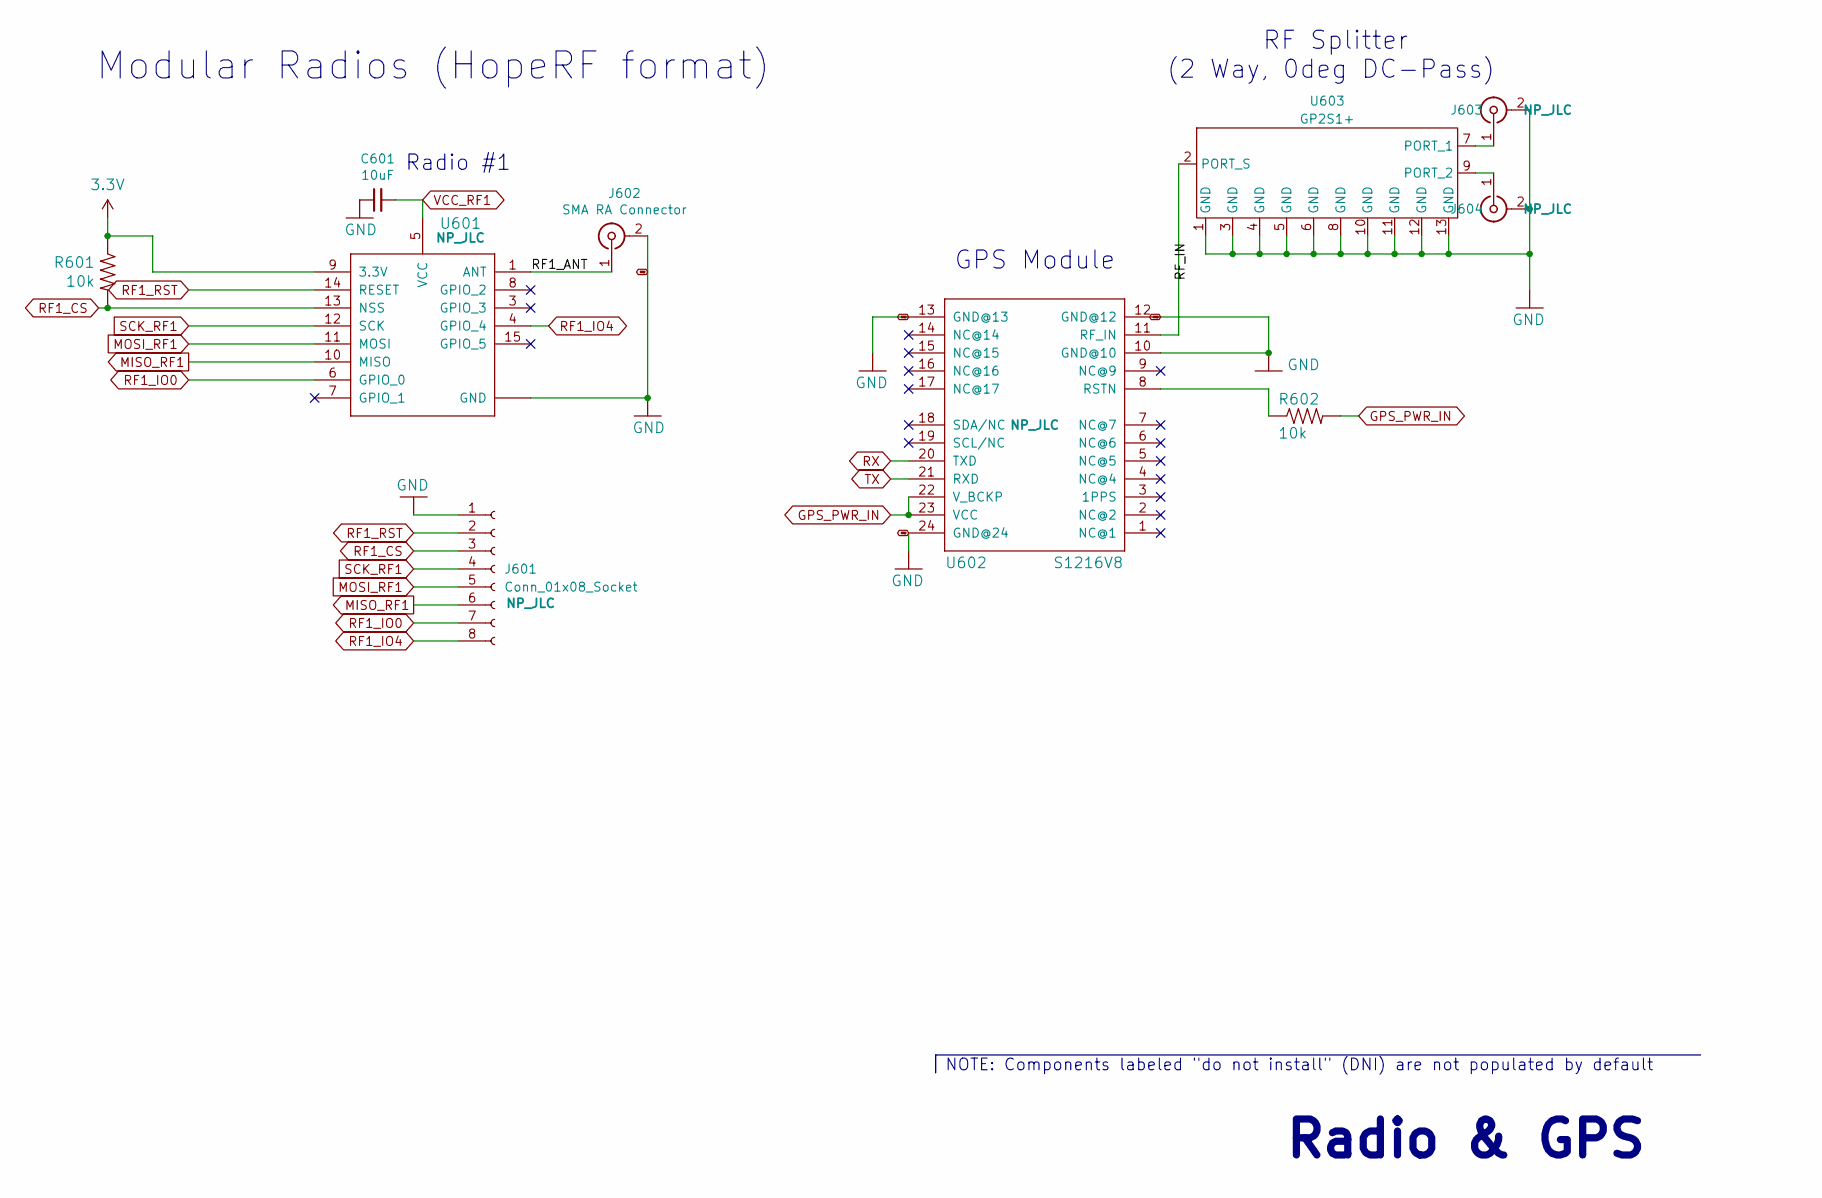
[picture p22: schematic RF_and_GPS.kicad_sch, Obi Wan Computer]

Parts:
C601: 10uF; C_0603_1608Metric; Manufacturer_Part_Number CL10A106MP8NNNC; LCSC C85713
J601: Conn_01x08_Socket; PinSocket_1x08_P2.54mm_Vertical
J602, J603, J604: SMA RA Connector; SAMTEC_MMCXV-J-P-HF-ST-EM1; Manufacturer_Part_Number MMCXV-J-P-HF-ST-EM1-ND
R601, R602: 10k; R_0603_1608Metric; Manufacturer_Part_Number ERJ3GEYJ103V; LCSC C169849
U601: RFM98PW; RFM95PW; Manufacturer_Part_Number RFM98PW
U602: S1216V8; S1216_24PIN_PACKAGE; Manufacturer_Part_Number S1216V8
U603: GP2S1+; DQ1225-12-1EP_3.0x3.0mm_P0.51mm; Manufacturer_Part_Number GP2S1+; LCSC C879828

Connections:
3.3V: R601.1, U601.9 (3.3V); also elsewhere on the board
/RF and GPS/RF1_ANT: J602.1 (In), U601.1 (ANT)
GND: C601.1, J601.1, J602.2 (Ext), J603.2 (Ext), J604.2 (Ext), U601.2 (GND), U601.16 (GND), U601.17 (GND), U602.10 (GND@10), U602.12 (GND@12), U602.13 (GND@13), U602.24 (GND@24), U603.1 (GND), U603.3 (GND), U603.4 (GND), U603.5 (GND), U603.6 (GND), U603.8 (GND), U603.10 (GND), U603.11 (GND), U603.12 (GND), U603.13 (GND); also elsewhere on the board
GPS_PWR_IN: R602.2, U602.22 (V_BCKP), U602.23 (VCC); also elsewhere on the board
MISO_RF1: J601.6, U601.10 (MISO); also elsewhere on the board
MOSI_RF1: J601.5, U601.11 (MOSI); also elsewhere on the board
unnamed: J603.1 (In), U603.7 (PORT_1)
unnamed: J604.1 (In), U603.9 (PORT_2)
unnamed: U602.11 (RF_IN), U603.2 (PORT_S)
unnamed: R602.1, U602.8 (RSTN)
RF1_CS: J601.3, R601.2, U601.13 (NSS); also elsewhere on the board
RF1_IO0: J601.7, U601.6 (GPIO_0); also elsewhere on the board
RF1_IO4: J601.8, U601.4 (GPIO_4); also elsewhere on the board
RF1_RST: J601.2, U601.14 (RESET); also elsewhere on the board
RX: U602.20 (TXD); also elsewhere on the board
SCK_RF1: J601.4, U601.12 (SCK); also elsewhere on the board
TX: U602.21 (RXD); also elsewhere on the board
VCC_RF1: C601.2, U601.5 (VCC); also elsewhere on the board

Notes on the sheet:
RF Splitter (2 Way, 0deg DC-Pass)
Modular Radios (HopeRF format)
Radio & GPS
NOTE: Components labeled "do not install" (DNI) are not populated by default
Radio #1
GPS Module

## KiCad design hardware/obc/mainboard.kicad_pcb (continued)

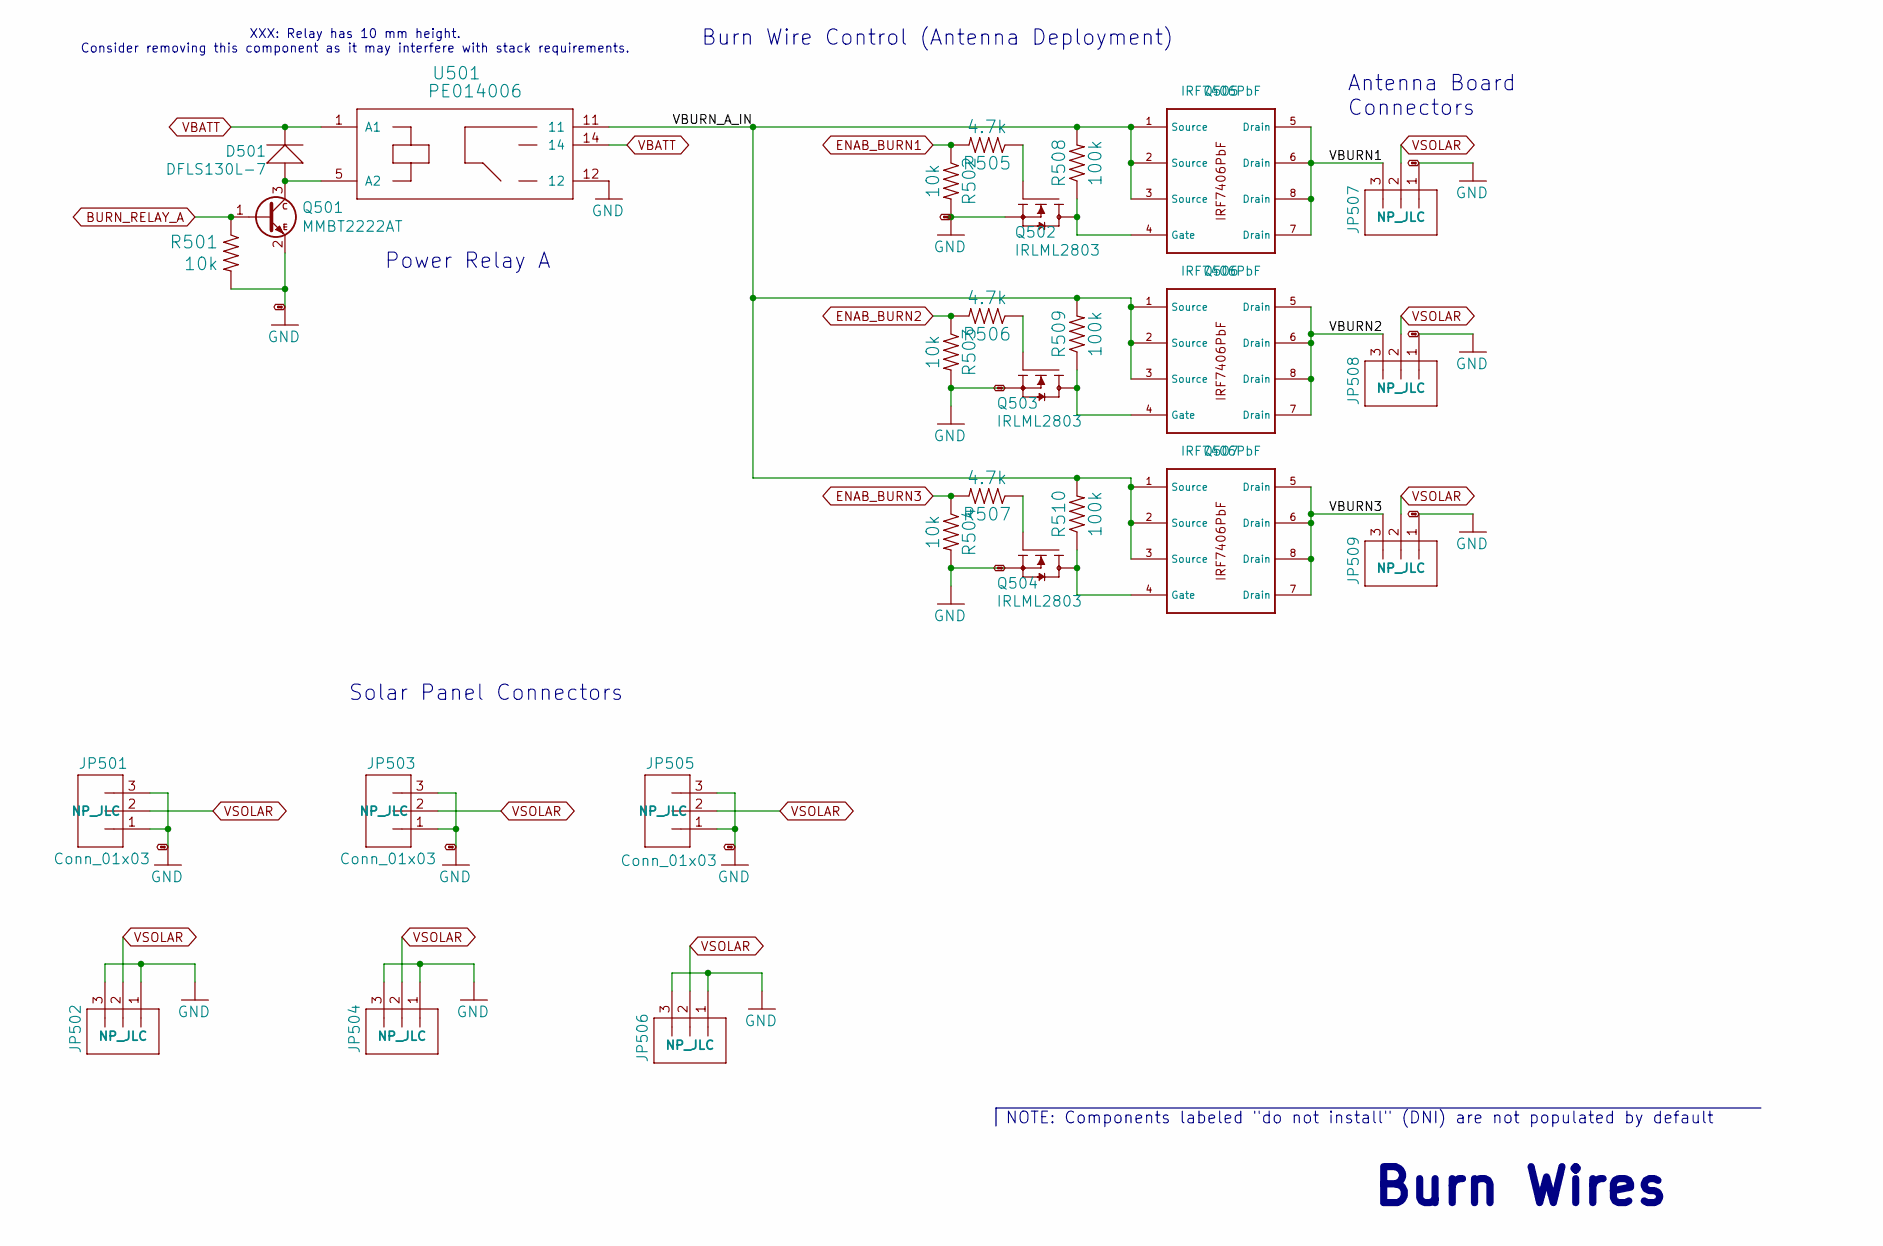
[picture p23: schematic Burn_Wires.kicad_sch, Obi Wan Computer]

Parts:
D501: DFLS130L-7; D_SOD-123; Manufacturer_Part_Number DFLS130L-7; LCSC C110493
JP501, JP502, JP503, JP504, JP505, JP506, JP507, JP508, JP509: Conn_01x03; CONN_22-11-2032_MOL; Manufacturer_Part_Number 0022112032
Q501: MMBT2222AT; SOT-23; Manufacturer_Part_Number MMBT2222ALT1G; LCSC C82460
Q502, Q503, Q504: IRLML2803; SOT-23; Manufacturer_Part_Number IRLML2803TRPBF; LCSC C2590
Q505, Q506, Q507: IRF7406PbF; SO-8_3.9x4.9mm_P1.27mm; Manufacturer_Part_Number IRF7406TRPBF; LCSC C169769
R501, R502, R503, R504: 10k; R_0603_1608Metric; Manufacturer_Part_Number ERJ3GEYJ103V; LCSC C169849
R505, R506, R507: 4.7k; R_0603_1608Metric; Manufacturer_Part_Number 0603WAF4701T5E; LCSC C23162
R508, R509, R510: 100k; R_0603_1608Metric; Manufacturer_Part_Number CRCW0603100KFKEC; LCSC C5369222
U501: PE014006; RELAY_PE014006_REV-SSE; Manufacturer_Part_Number PE014006 TE

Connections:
/Burn Wires/VBURN1: JP507.3, Q505.5 (Drain), Q505.6 (Drain), Q505.7 (Drain), Q505.8 (Drain)
/Burn Wires/VBURN2: JP508.3, Q506.5 (Drain), Q506.6 (Drain), Q506.7 (Drain), Q506.8 (Drain)
/Burn Wires/VBURN3: JP509.3, Q507.5 (Drain), Q507.6 (Drain), Q507.7 (Drain), Q507.8 (Drain)
/Burn Wires/VBURN_A_IN: Q505.1 (Source), Q505.2 (Source), Q505.3 (Source), Q506.1 (Source), Q506.2 (Source), Q506.3 (Source), Q507.1 (Source), Q507.2 (Source), Q507.3 (Source), R508.2, R509.2, R510.2, U501.11
BURN_RELAY_A: Q501.1 (B), R501.1; also elsewhere on the board
ENAB_BURN1: R502.1, R505.2; also elsewhere on the board
ENAB_BURN2: R503.1, R506.2; also elsewhere on the board
ENAB_BURN3: R504.1, R507.2; also elsewhere on the board
GND: JP501.1, JP501.3, JP502.1, JP502.3, JP503.1, JP503.3, JP504.1, JP504.3, JP505.1, JP505.3, JP506.1, JP506.3, JP507.1, JP508.1, JP509.1, Q501.2 (E), Q502.2 (S), Q503.2 (S), Q504.2 (S), R501.2, R502.2, R503.2, R504.2, U501.12; also elsewhere on the board
unnamed: D501.A, Q501.3 (C), U501.5 (A2)
unnamed: Q502.3 (D), Q505.4 (Gate), R508.1
unnamed: Q502.1 (G), R505.1
unnamed: Q503.3 (D), Q506.4 (Gate), R509.1
unnamed: Q503.1 (G), R506.1
unnamed: Q504.3 (D), Q507.4 (Gate), R510.1
unnamed: Q504.1 (G), R507.1
VBATT: D501.C, U501.1 (A1), U501.14; also elsewhere on the board
VSOLAR: JP501.2, JP502.2, JP503.2, JP504.2, JP505.2, JP506.2, JP507.2, JP508.2, JP509.2; also elsewhere on the board

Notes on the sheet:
Antenna Board Connectors
Burn Wires
XXX: Relay has 10 mm height. Consider removing this component as it may interfere with stack requirements.
Burn Wire Control (Antenna Deployment)
Solar Panel Connectors
Power Relay A
NOTE: Components labeled "do not install" (DNI) are not populated by default


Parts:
C201, C202, C203, C204: 10nF; C_0603_1608Metric; Manufacturer_Part_Number CL10B103KB8NNNC; LCSC C1589
Q201, Q202, Q205, Q206: BSS138DWQ-7; SOT-363_SC-70-6; Manufacturer_Part_Number BSS138DWQ-7; LCSC C3280240
Q203, Q204, Q207, Q208: MBT2222ADW1T1; SOT-363_SC-70-6; Manufacturer_Part_Number MBT2222ADW1T1G; LCSC C157366
Q209: MMDT2907; SOT-363_SC-70-6; Manufacturer_Part_Number MMDT2907AQ-7-F; LCSC C526684
R201, R202, R211, R212: 100K; R_0603_1608Metric; Manufacturer_Part_Number CRCW0603100KFKEC; LCSC C5369222
R203, R204, R213, R214: 680; R_0603_1608Metric; Manufacturer_Part_Number CRCW0603680RJNEA; LCSC C4244464
R205, R206, R207, R209, R215, R216, R217, R219: 10k; R_0603_1608Metric; Manufacturer_Part_Number ERJ3GEYJ103V; LCSC C169849
R208, R210, R218, R220: 200K; R_0603_1608Metric; Manufacturer_Part_Number ERA3AEB204V; LCSC C473261
R221, R222, R223, R224, R230: 0; R_0603_1608Metric; Manufacturer_Part_Number MCT06030Z0000ZP500; not fitted
R225: 0; R_0603_1608Metric; Manufacturer_Part_Number MCT06030Z0000ZP500; LCSC C2654002
R226: 4.7k; R_0603_1608Metric; Manufacturer_Part_Number 0603WAF4701T5E; LCSC C23162
R227, R228: 1K; R_0603_1608Metric; Manufacturer_Part_Number CRCW06031K00FKEAC; LCSC C844746

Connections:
3.3V: R201.1, R202.1, R205.1, R206.1, R207.1, R209.1, R211.1, R212.1, R215.1, R216.1, R217.1, R219.1; also elsewhere on the board
GND: C201.2, C202.2, C203.2, C204.2, Q201.1 (S2), Q201.4 (S1), Q202.1 (S2), Q202.4 (S1), Q205.1 (S2), Q205.4 (S1), Q206.1 (S2), Q206.4 (S1); also elsewhere on the board
MISO: Q209.6 (C1), R230.2; also elsewhere on the board
MISO_RF1: R225.2, R230.1; also elsewhere on the board
MOSI: R228.1; also elsewhere on the board
MOSI_RF1: R228.2; also elsewhere on the board
unnamed: Q201.6 (D1), Q203.5 (B2), R203.2, R205.2
unnamed: Q201.2 (G2), Q201.3 (D2), R201.2
unnamed: C201.1, Q201.5 (G1), R208.2
unnamed: Q202.6 (D1), Q204.5 (B2), R204.2, R206.2
unnamed: Q202.2 (G2), Q202.3 (D2), R202.2
unnamed: C202.1, Q202.5 (G1), R210.2
unnamed: Q203.2 (B1), R203.1
unnamed: Q204.2 (B1), R204.1
unnamed: Q205.6 (D1), Q207.5 (B2), R213.2, R215.2
unnamed: Q205.2 (G2), Q205.3 (D2), R211.2
unnamed: C203.1, Q205.5 (G1), R218.2
unnamed: Q206.6 (D1), Q208.5 (B2), R214.2, R216.2
unnamed: Q206.2 (G2), Q206.3 (D2), R212.2
unnamed: C204.1, Q206.5 (G1), R220.2
unnamed: Q207.2 (B1), R213.1
unnamed: Q208.2 (B1), R214.1
unnamed: Q209.2 (B1), R226.1
unnamed: Q209.1 (E1), R225.1
RF1_CS: R226.2; also elsewhere on the board
SCK: R227.2; also elsewhere on the board
SCK_RF1: R227.1; also elsewhere on the board
SCL: Q203.1 (E1), Q203.3 (C2), Q204.1 (E1), Q204.3 (C2), R221.2, R223.2; also elsewhere on the board
SCL_IMU: Q203.4 (E2), Q203.6 (C1), R207.2, R208.1, R221.1; also elsewhere on the board
SCL_PWR: Q204.4 (E2), Q204.6 (C1), R209.2, R210.1, R223.1; also elsewhere on the board
SDA: Q207.1 (E1), Q207.3 (C2), Q208.1 (E1), Q208.3 (C2), R222.2, R224.2; also elsewhere on the board
SDA_IMU: Q207.4 (E2), Q207.6 (C1), R217.2, R218.1, R222.1; also elsewhere on the board
SDA_PWR: Q208.4 (E2), Q208.6 (C1), R219.2, R220.1, R224.1; also elsewhere on the board

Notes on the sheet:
These novel bus protection circuits prevent traditional I2C/SPI failure modes where a single slave failure can disable the entire bus. Learn more: https://doi.org/10.36227/techrxiv.15166620 By default, slave clock and/or data lines can be held low and the Master (SAMD51) will still be able to commu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
SPI Bus Protection - Radio 1
NOTE: Components labeled "do not install" (DNI) are not populated by default
NOTE
XXX: Low LCSC stock of component (BSS138DWQ-7; Q12A, Q7A, etc.) Potentially research alternatives.
Bus Protection
I2C Bus Protection - Power Monitor
I2C Bus Protection - IMU
Bus Protection - Bypass Jumpers



Board: 6 copper layers, 95.9 x 90.2 mm, 214 parts (14 on the bottom side), 153 nets.

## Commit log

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2024-05-02 obc: bring in design work in progress
    I've worked on these design files for the past few weeks on a different repository, but this is the beginning of the effort to unify all of our electronic design work into one repository.
    [Avionics.kicad_sch, Burn_Wires.kicad_sch, Bus_Protection.kicad_sch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]
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2024-05-04 obc: schematic cleanup and wiring
    Demarcated NC pins, added High-Rel connectors, cleaned up schematic legibility, and added bus protection for stacking signals SDA & SCL.
    [Avionics.kicad_sch, Bus_Protection.kicad_sch, Connectors.kicad_sch]
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2024-05-10 obc: schematic editing and footprint development
    Deleted irrelevant SD-related circuits and pins. Created new & modified existing connector and inductor footprints. Added new components (Bat Charger, High-Rel Connector, etc.)
    [Avionics.kicad_sch, Burn_Wires.kicad_sch, Bus_Protection.kicad_sch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]
2024-05-10 obc: BOM component verification
    Verified part numbers, availability, values, footprints, etc. of components. Next steps involve verifying footprints and potentially researching some alternative components.
    [Avionics.kicad_sch, Burn_Wires.kicad_sch, Bus_Protection.kicad_sch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]
2024-05-10 footprints: restore solarbit footprints
    These were deleted in error by the previous commit.
2024-05-13 ZM panel revision (v5)
    I added 3D models for all the solar bits' footprint, the 8x23 23x25 and 23x42, so that the ZM circuit board could be view in 3D. This allows to check for any errors we couldn't previously visualize along with giving us a sense to what the completed board should look like. Note that the next steps would be Mr. Lyle making sure there are no errors then potentially ordering the board.
2024-05-13 obc: footprint editing and schematic revision
    Added GPS21+ and edited inductor footprints. Edited schematic circuitry and re-annotated schematic components.
    [Avionics.kicad_sch, Burn_Wires.kicad_sch, Bus_Protection.kicad_sch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]
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2024-05-15 obc: BOM editing
    Edited the DNI status of several components to be more reflective of our obc setup plans.
    [Avionics.kicad_sch, Burn_Wires.kicad_sch, Bus_Protection.kicad_sch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]
2024-05-17 obc: preliminary board layout
    Entered design rules and grouped components according to schematic. Slightly edited BOM.
    [Avionics.kicad_sch, Burn_Wires.kicad_sch, Bus_Protection.kicad_sch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]
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2024-05-22 obc: begun formal layout
    Organized the components of the first two schematic pages into formal layout and switched out connector components. Introduced step files for previously developed footprints.
    [Avionics.kicad_sch, Bus_Protection.kicad_sch, Connectors.kicad_sch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]
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2024-05-23 obc: formal placement and 3D models entered
    Placed components of onto board, orienting them for ease of trace creation. Entered 3D models of footprints into KiCad for design verification and aesthetics.
    [Burn_Wires.kicad_sch, Power.kicad_sch, mainboard.kicad_pcb]
2024-05-24 obc: component reorganization
    Blanket shrunk silk text, edited connector placement, switched out molex connectors, entered step files, and reorganized to increase area-efficiency.
    [Burn_Wires.kicad_sch, mainboard.kicad_pcb]
2024-05-28 obc: preliminary layout complete
    Finished preliminary layout of components onto pcb. Entered revised SMA connector into design, however, there is confusion with regards to board cutouts.
    [RF_and_GPS.kicad_sch, mainboard.kicad_pcb]
2024-05-28 obc: Update board outline and MMCXV 3d model
    The model was upside down; the board edge lines were not connected.
    [mainboard.kicad_pcb]
2024-05-29 obc: design review 5/28 implemented
    Entered step models, adjusted pin clearances, and edited footprints.
    [Burn_Wires.kicad_sch, Connectors.kicad_sch, mainboard.kicad_pcb]
2024-05-30 obc: various changes from design review
    - change 1008 inductor footprint to one from kicad library
    - change 'default class' design rules to match board design rules
    - back-annotate from layout to board
    [Power.kicad_sch, mainboard.kicad_pcb]
2024-06-04 obc: entered footprint and routed traces in a test subsection
    Made harwin battery connector vertical and routed traces around U405 component.
    [Connectors.kicad_sch, mainboard.kicad_pcb]
2024-06-04 obc: edited test subsection routing
    Adjusted test routing to utilize vias and designated signal layers.
    [mainboard.kicad_pcb]
2024-06-04 obc: further test subsection routing adjustments
    Added "long" traces connecting to microcontroller (which was previously considered too ambitious for test routing).
    [mainboard.kicad_pcb]
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2024-06-05 GPS Design 3D Models
    This is all the changes I did in May for GPS, LNA, and antenna. This would include 3D models, wiring, and any other changes need for the 3 PCBs. Notice that none of the DRCs are passed. This will be worked on later in the future when we choose which design is wanted and we change the clearance levels.
2024-06-05 obc: component reorganization
    Adjusted component organization by GND & GNDREF power inputs and created planes accordingly.
    [mainboard.kicad_pcb]
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2024-06-06 obc: reorganization, power plane creation, and power connection
    Adjusted placement by power input. Created power planes in layer 2 (In.1). Added ~250 vias connecting pads to power & gnd planes.
    [mainboard.kicad_pcb]
2024-06-07 obc: power connection cleanup
    Decreased track length to vias and centered all vias in pad. Updated schematic title blocks, edited 3D models.
    [Avionics.kicad_sch, Burn_Wires.kicad_sch, Bus_Protection.kicad_sch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]
2024-06-07 obc: adjusted component values
    Aligned component values to proper orientation where necessary. Slight adjustments to organization and gnd plane drawing.
    [mainboard.kicad_pcb]
2024-06-08 obc: slight adjustments
    Edited radio footprint and added thick pwr trace to connect vburna on relay to pour. Slight adjustments to via centering.
    [mainboard.kicad_pcb]
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2024-06-10 obc: more test routing
    Getting a feel for the problem space regarding traces by way of test routing.
    [mainboard.kicad_pcb]
2024-06-11 obc: more preliminary routing
    Still exploring problem space regarding routing, ~100 routed nets added.
    [Connectors.kicad_sch, mainboard.kicad_pcb]
2024-06-11 Adjust zone fills for burnwire
    Attempt to lower resistance.
    [mainboard.kicad_pcb]
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2024-06-18 obc: minor edits regarding routing
    ~30 more nets routed. Discovered many problems w existing traces. Lot of cleanup required.
    [Power.kicad_sch]
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2024-06-28 obc: Updates from 6/28 design review and small fixes
    - various board layout work to clear DRC errors, better connect planes,
    delete hanging tracks, etc.
    - Set radio thermal hole net names to eliminate DRC errors
    - Straightened some traces and improved clearances
    - Migrated legacy format symbol library mainboard.lib ->
    mainboard.kicad_sym. Still needs unification with other NyanSat
    symbol libraries.
    - Renumbered LTC4121 symbol pins from e.g. P$1 to just '1' to match
    KiCad conventions.
    - Moved LTC4121 to KiCad QFN 16 0.5 built-in symbol
    [Avionics.kicad_sch, Burn_Wires.kicad_sch, Bus_Protection.kicad_sch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]
2024-06-29 obc: near final adjustments
    Spread out traces where necessary. Adjusted routing, placement, and pour definitions. Reached 0 nets unrouted. Replaced tp101 w/ rc termination network for flash_sck. Adjusted placement to allow access to bladed connector.
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2024-06-30 obc: power path and routing changes
    - Widen all the critical power paths
    - Flip C416/R225 to improve routing
    - Pin swap GND/GNDREF on RBF jumpers to improve routing
    - Route USB D+/D- in differential fashion
    - Correct schematic: test point that was removed was not removed
    from schem.
    Primary known TODO:
    - Add more vias to critical power paths
    - Route RF
    - BOM fixes
    [Avionics.kicad_sch, Burn_Wires.kicad_sch, Bus_Protection.kicad_sch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]
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2024-06-30 obc: remove superfluous schem XXX comments
    All were reviewed.
    - Some didn't matter - entire comment removed
    - Some were just notes, not action items - XXX notation removed
    Two items noted do have implications, though:
    - WDT rst pulldown value is incorrect.
    - I2C pulls are missing (though this could be ignored).
    [Avionics.kicad_sch, Burn_Wires.kicad_sch, Bus_Protection.kicad_sch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]
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2024-06-30 obc: corrections to watchdog circuit
    Per MAX706 datasheet, tie MR# high instead of to WDO#.
    Also, use a 680 ohm resistor to drive microcontroller RST#
    signal; the original design was a 10k/10k divider which would
    have put it midrail; this will swing 95% of the way now and
    should be good enough.
    [Avionics.kicad_sch]
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2024-07-01 obc: cleanups of items identified by DRC
    We had a few shorts from where any-angle mode or dropping vias
    resulted in badness.
    Identified another issue: groundpath through GND_REF -> GND
    is very narrow and requires significant help.
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2024-07-01 obc: pre-order checkpoint
    Have uploaded the entire board to JLC without too much heartburn.
    Things remaining to check:
    - Thermal path on radio pads shows black in 3d view
    - SOT-363 Transistors that are hard to order -- BSS138DWQ-7,
    MMDT2907.
2024-07-01 obc: remove errant "too much resistance" comment
    Was fixed in d3ba5395cb556b76f2be0f4a4653125f56a0b98e .
    [Avionics.kicad_sch]
2024-07-01 obc: substitute transistors based on study of datasheets
    We have struggled with availability and made these substitutions.
    Same footprint, so layout doesn't change:
    ON BSS138DWQ-7-F -> Nexperia BSS138PS,115
    ON MMDT2907AQ-7-F -> Nexperia BC857BS,115
    [Bus_Protection.kicad_sch]
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2024-10-04 obc: errata: add more silk errata
    Relating to insufficient connector labelling and possible coordinate
    system problems
2024-10-16 obc: errata: GPS related problems
    - Difficult to insert MMCXV connectors
    - Unable to make GPS work
2024-10-16 obc: errata: ltc4121 might hit current limit
2024-10-22 obc: moved components from avionics schem
    Move the stacking connector, holes to the connectors page.
    This will make space for changes to microcontroller to fix errata.
    [Avionics.kicad_sch, Burn_Wires.kicad_sch, Bus_Protection.kicad_sch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]
2024-10-24 obc: errata: flash chips are not hooked to valid SPI
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2024-10-26 cpb: fix net name typos, assign footprints
    Fix errors found by DRC.
    Assign footprints so that it is possible to go to layout.
    Select crystal for UART.
    [cpb.kicad_sch]
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2024-11-02 nyansat-symbols: correct footprint for MAX22200
2024-11-02 cpb: correct problems detected by ERC
    Mostly duplicate/misnamed reference identifiers.
    [cpb.kicad_sch]
2024-11-02 cpb: fix connectors and other small details
    [cpb.kicad_sch]
2024-11-02 bareboard: design rules
    Track widths, via sizes, teardrops, clearances, connectivity.
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2024-11-18 obc: update fp-lib-table sse_footprints vs nyansat-footprints
    This is unfortunate. There is a legacy sse footprints library
    that needs to be coalesced.
    Thanks to Porter and Luke for noticing this problem.
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2024-11-21 hardware/cpb: moved u6 and added bypass capacitors
    Untangled components around u6 as well as flipped top right corner connectors. Bypass capacitors added for U1-U9.
    [cpb.kicad_pcb]
2024-11-21 footprints: update RPI02W
    - Pin 1 was not in correct orientation
    - Holes were rounded to 1mm in position; wouldn't have lined up
    - Add STEP model.
2024-11-21 cpb: many, many fixes
    - Move components to bottom to match design intent
    - Adjust AP62305 to hopefully have correct pinout
    - Replace manual RBF jumper with solder jumper: just not enough room
    - High level adjustment to placement to ease layout.
    [FourFullBridges.kicad_sch, I2CProtection.kicad_sch, PairPowerSwitches.kicad_sch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]
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2024-11-22 cpb: continued work towards layout
    - Adjust schematic; add datasheets, correct switcher output. Additional
    validation required.
    - Adjust text.
    - Add graphics
    - Update design rules
    - Perform an initial DRC in schematic & in layout.
    [FourFullBridges.kicad_sch, cpb.kicad_pcb, cpb.kicad_sch]
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2024-11-23 cpb: SDA/SCL were not connected to I2C-SPI
    Wrong net names were used; the protection circuit moved into the
    subcircuit and the names in the toplevel schematic were not updated.
    [cpb.kicad_sch]
2024-11-23 cpb: routing in progress
    - Adjust layout for easier routing.
    - Pin swap clamping diodes to simplify routing.
    - Route the high power nets
    - Adjust plane pours.
    [FourFullBridges.kicad_sch, cpb.kicad_pcb]
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2024-11-26 cpb: property updates, part numbers
    RN2 part number was wrong.
    Set DNP components value to "DNP" to aid ordering.
    [cpb.kicad_sch]
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2024-12-01 hardware/obc: errata: watchdog timer producing incorrect/unexpected results when WDI not toggled
    when the WDT was not toggled using the WDI pin, RESET# would not produce reset pulses, indicating that we'd be stuck in an infinite reset loop. however, on power up, it behaved according to how the datasheet said it should (Figure 3 on datasheet)
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2024-12-12 OBC/SSE_Footprints: GPS21+ edits
    changed GPS21+ footprint pads to be numbered counter-clockwise, to address GPS-related errata
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2024-12-13 hardware/obc: errata: radio missing pin 1 marker on board
2024-12-17 cpb: add errata (Q3 missing base resistor)
2024-12-17 OBC: Continuing work towards the next revision
    - moved Jtag to Avionics page
    - re-aligned and removed excess text
    - flipped watchdog to make +3.3v face up
    - cleaned up VREG pins, crystal, SWCLK, SWDIO, and watch dog connections
    - fixed MRAM symbol
    - changed USB_D +/- resistor values
    - spaced out schematics on power and burn wire pages
    - fixed GNDREF connection for J302
    [Avionics.kicad_sch, Burn_Wires.kicad_sch, Connectors.kicad_sch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]
2024-12-28 cpb: Update errata; power switches are slow
2025-01-04 obc: errata: Solar charger doesn't always work
2025-01-04 obc: update errata to describe solar charger issue
2025-01-04 cpb: errata: may want supply on ADC headers
2025-01-07 hardware/cpb: RN vias and 2.2 nF capacitor fixed.
    Vias on all RNs are now have a proper fanout and C37 was moved and now connects between the gate and VBATT+.
    [FourFullBridges.kicad_sch, I2CProtection.kicad_sch, PairPowerSwitches.kicad_sch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]
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2025-01-09 cpb: errata: Note that there is a missing SPI pullup resistor
    Also clarify other errata.
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2025-01-09 OBC: Continuing work towards the next revision
    - Cleaned up text on Avionics Page
    - Changed some descriptions and cleaned up text on Power Page
    - Changed Power Relay A schematic to one from PCB
    - Changed R120 and R401 changed from 107k to 34.8k and changed R121 and R404 from 0 to 10k and R127 and R419 from 3.01k to 3.83k (Solar Chargers Page)
    - Checked R303 and R304 resistor value and believe 27 is correct
    [Avionics.kicad_sch, Burn_Wires.kicad_sch, Connectors.kicad_sch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]
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2025-01-14 obc: power sup: fix mistake, add theory, clean up
    1. During component selection, FET drain and sources were reversed
    (fixed).
    2. Was able to make page much cleaner.
    3. Rearrange power page, add some XXX comments.
    [Power.kicad_sch, Power_Supervisor_and_Watch_Dog.kicad_sch]
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2025-01-14 hardware/cpb: changed from european to american symbols.
    RN parts still are european for now. Changed via TextEdit replace all tool. Device:R --> Device:R_US
    [FourFullBridges.kicad_sch, I2CProtection.kicad_sch, PairPowerSwitches.kicad_sch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]
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2025-01-18 obc: changed flash memory to PSRAM
    - Fixed MRAM symbol
    - Removed Flash memory for new PSRAM
    - Changed labels on Avionics page to match format
    - Added another 0.1uF capacitor to VRAG pins
    [Avionics.kicad_sch, Connectors.kicad_sch, mainboard.kicad_sch]
2025-01-23 obc: Fixed errors from design review
    - Gave proper attribution on all pages
    - Spread out components on Avionics page
    - Changed GPS power circuit
    - Added a DNP resistor in between VBATT and VWATCHEDRAIL
    - Added various other part numbers on Power Supervisor and Watch Dog Page
    - Changed Power Supervisor and Watch Dog Page to page 3
    [Avionics.kicad_sch, Burn_Wires.kicad_sch, Bus_Protection.kicad_sch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]
2025-01-27 hardware/cpb: finished revisions
    did all things specified on Errata file for cpb;
    [FourFullBridges.kicad_sch, PairPowerSwitches.kicad_sch, cpb.kicad_sch]
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2025-02-04 obc: Fixed second design review, and fixed up BOM
    - added layout comments on schematic
    - fixed various comments
    - added many LCSC # for components
    [Avionics.kicad_sch, Burn_Wires.kicad_sch, Bus_Protection.kicad_sch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]
2025-02-06 cpb: revert pcb layout; a component was accidentally moved
2025-02-10 hardware/cpb: fixed BOM issues and placed new components down.
    C28 and C31 were given an 0805 footprint, J8 was given a footprint, placed testpoints and new LED.
    [cpb.kicad_sch]
2025-02-11 hardware/cpb: moved testpoints again
    fixed the location of the testpoints so that they are on the correct power planes.
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2025-02-13 hardware/cpb: edits from design review
    - Nudge text away from board edge.
    - Add missing text to ADC connectors.
    - Improve guard ring around reference voltage.
    - Move test point text to bottom to reflect most common use case.
    - Slight nudges for text and layout.
    - Update numbering to revision A, dates to 24-25.
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2025-03-12 obc: rename power nets for sanity
    We've been confused by this for too long.
    GNDREF -> PACKNEG
    VCHRG -> PACKPOS
    VBATT -> VRAIL
    VBATT_SENSE -> INH_POS
    Also add an OBC power subsystem diagram.
    [Avionics.kicad_sch, Burn_Wires.kicad_sch, Connectors.kicad_sch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]
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2025-03-17 obc: changed burn wire connectors
    - removed unecescary wires on PACPOS
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2025-03-25 obc: final review of BOM
    - fixed duplicate parts
    - created new footprint for solar charger inductors
    - changed LCSC part number for red LED because it no longer existed
    [Avionics.kicad_sch, Burn_Wires.kicad_sch, Bus_Protection.kicad_sch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]
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2025-03-27 obc: BOM and schematic cleanup
    - remove unused fields
    - remove incorrect datasheets
    - fix a connector 'value' field (CONx02 instead of x05)
    - add documentation to power supervisor page
    This is in preparation for a comprehensive review pass by me.
    In the layout, some issues were identified (QSPI_* pins routed
    suboptimally, silkscreen on pads, and some layer reduction could
    take place. Bouncing this back to Luke for further work before
    my review pass there.
    [Avionics.kicad_sch, Burn_Wires.kicad_sch, Bus_Protection.kicad_sch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]
2025-03-27 obc: cleaned up BOM and re-routed MRAM and PSRAM
    - cleaned up notes that no longer applied and changed some LCSC part numbers
    - Gave QSPI_CLK a better route
    [Connectors.kicad_sch, Power.kicad_sch, Power_Supervisor_and_Watch_Dog.kicad_sch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]
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2025-04-03 ob: revised BOM and cleaned up PCB traces
    - fixed BOM issues noticed
    - added 2 extra capacitors on vwatchedrail and near 3.3v regulator
    - cleaned up traces and did layer reduction
    - moved whole watchdog circuit to a better location so all components can be close together
    [Avionics.kicad_sch, Burn_Wires.kicad_sch, Bus_Protection.kicad_sch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]
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2025-04-04 obc: design review and corrections
    - text cleanup, put components on grid
    - Re-route RF power network for radio to get thicker traces and lower
    impedance.
    - Route RF connections for GPS (controlled impedance)
    - Lots of straightening and spreading traces and improving pours
    (especially power paths).
    - Swap pinning of RBF jumper to reduce the possible downsides of
    any shorts or misconnections (don't put pack+ and pack- together on
    the connector)
    - geographical reannotate
    - improve placement of a couple of bypass caps
    - Adjust 10uF solar input capacitors to be 35V rated so as to not
    limit input voltage.
    - fix pinning of RF splitter
    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
    [Avionics.kicad_sch, Burn_Wires.kicad_sch, Bus_Protection.kicad_sch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]
2025-04-06 obc: correct footprint error (1806 -> 1006)
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2025-04-17 obc: Added errata after initial AF board bringup
